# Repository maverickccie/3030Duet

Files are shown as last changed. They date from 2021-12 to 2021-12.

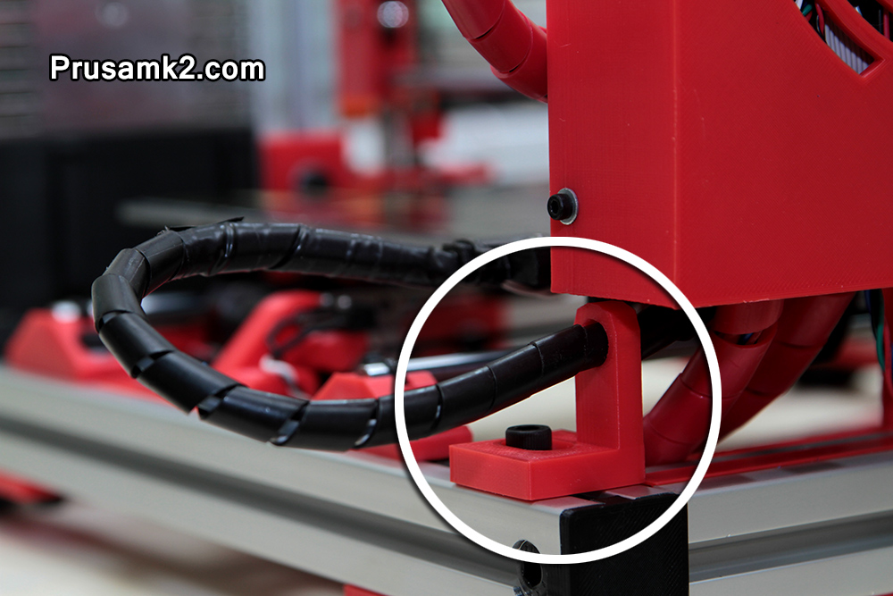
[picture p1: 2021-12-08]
Part STLs/Improved Parts from PrusaMK2.com/Haribo 3030_Cable_Guide/Photo.jpg

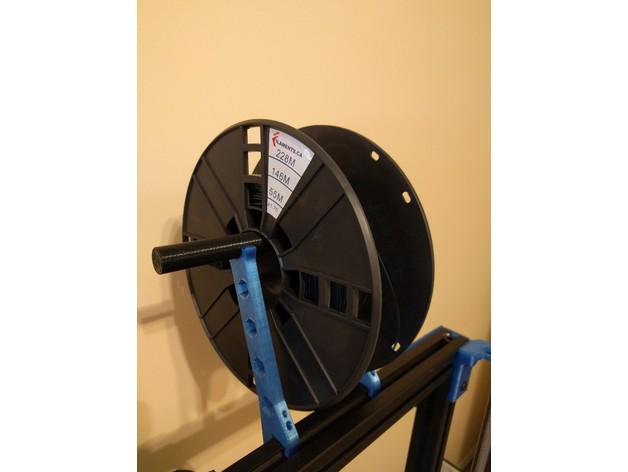
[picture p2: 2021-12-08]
Part STLs/SpoolHolders/Spool_Holder_for_3030_Extrusion/images/f4c73352651c89bbb47f65c14cc03cf2_preview_featured.jpg

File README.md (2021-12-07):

# My 3030 Duet baseed MK2.5

Better then a stock Prusa MK2.5 in so many ways

## Introduction

Welcome my project page!

## Thanks to 

### CNCKitchen

I used this his guide to move to the Duet V3 mini: https://www.cnckitchen.com/blog/prusa-mk25s-duet-3-mini-5-conversion

Dude you rock!!!!!

### Prusamk2users

The orginal conversion to Haribo 3030 came from here: https://github.com/PrusaMK2Users/3030_Haribo_Edition

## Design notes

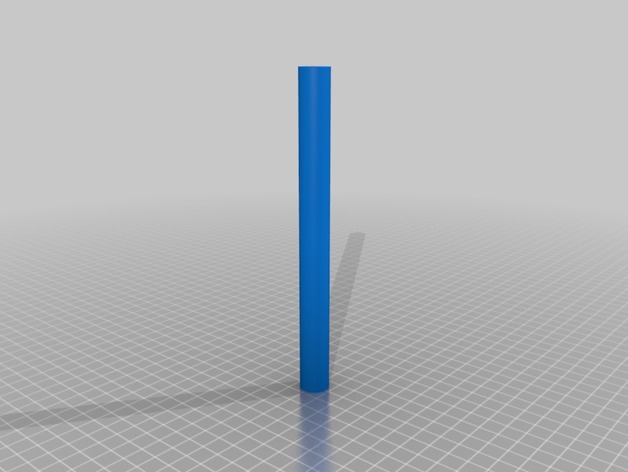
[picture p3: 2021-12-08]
Part STLs/SpoolHolders/Spool_Holder_for_3030_Extrusion/images/fe1c89c3e8150db4dd0982f04f4783a8_preview_featured.jpg

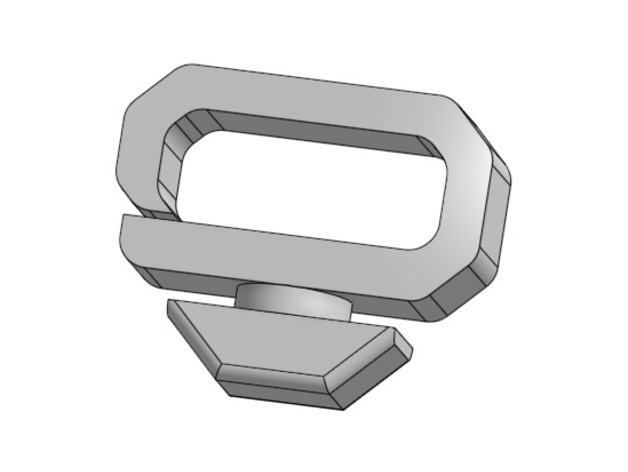
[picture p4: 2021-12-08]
Part STLs/CableClips/3030_Extrusion_Profile_Cable_Clip/images/18c306208e1527c0a5ba9f1ea7bc6678_preview_featured.jpg

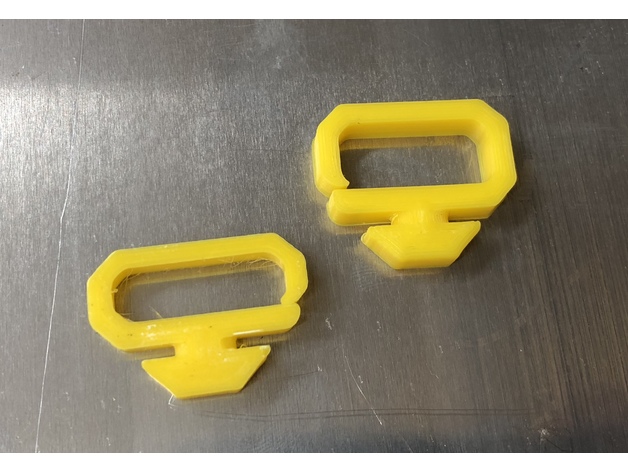
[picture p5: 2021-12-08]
Part STLs/CableClips/3030_Extrusion_Profile_Cable_Clip/images/cf8a90efcba08733e2580e20ebf21c80_preview_featured.jpg

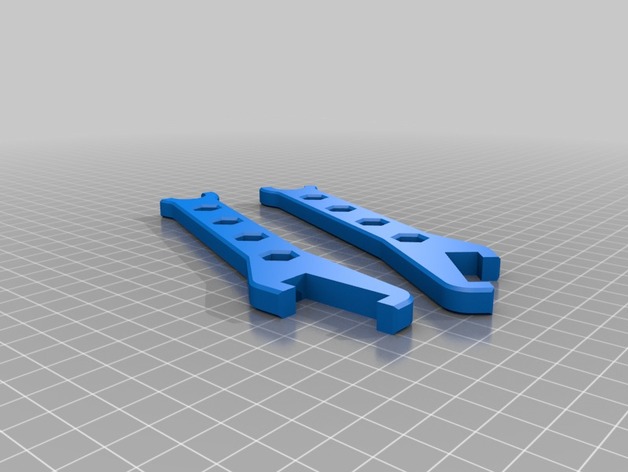
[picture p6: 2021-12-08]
Part STLs/SpoolHolders/Spool_Holder_for_3030_Extrusion/images/9926562ceaf5244885a4c4ae6ae50522_preview_featured.jpg

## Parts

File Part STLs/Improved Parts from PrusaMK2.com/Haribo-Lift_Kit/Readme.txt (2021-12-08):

These can be printed (4) and placed under each corner raising your Haribo 40mm off your work surface allowing you to easily to reach under your printer to clean up debris.

Square surface top, round surface to mate with rubber anti vibration pads.

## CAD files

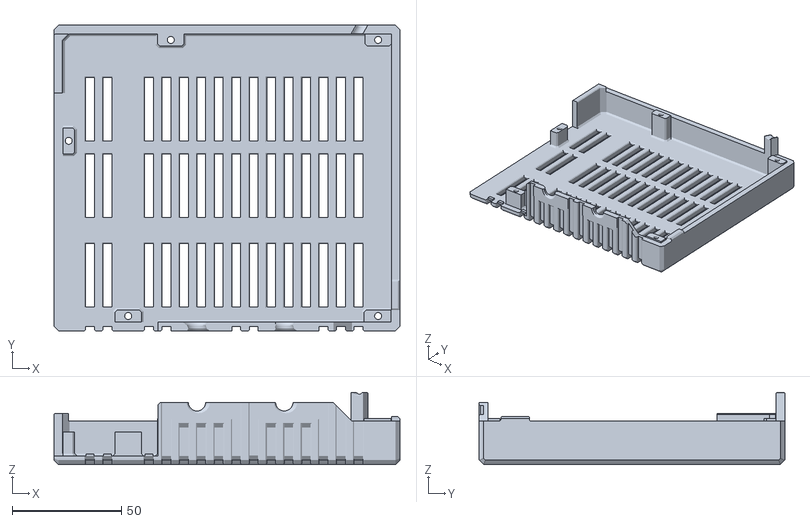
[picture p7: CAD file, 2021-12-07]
CNCKitchen/Box_Top.stl
158.5 x 140.0 x 33.0

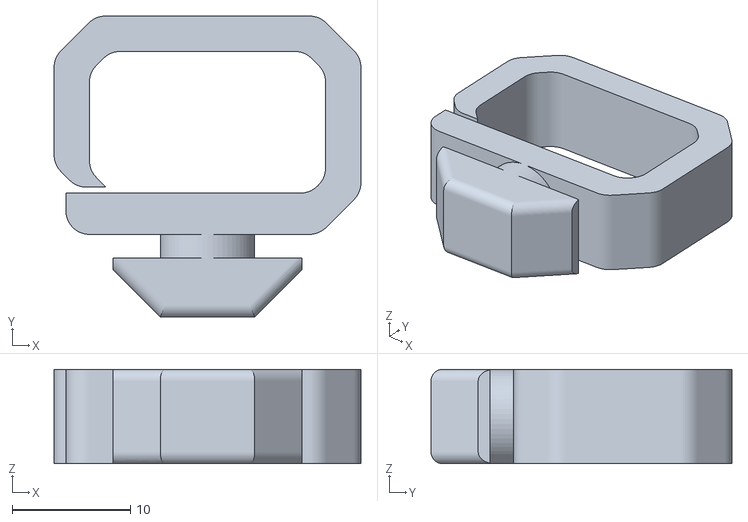
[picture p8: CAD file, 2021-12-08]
Part STLs/CableClips/3030_Extrusion_Profile_Cable_Clip/files/3030_cable_clip_12mm.stl
26.0 x 25.5 x 8.00

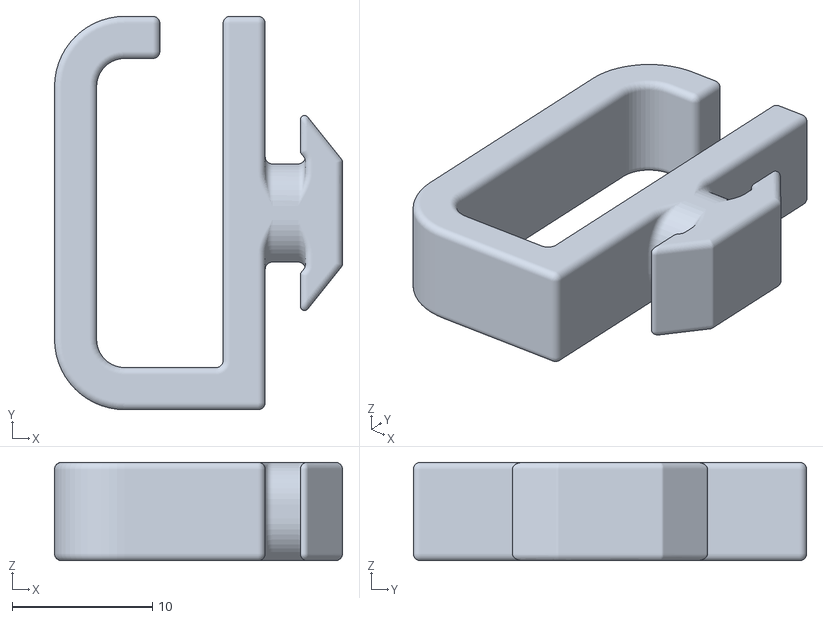
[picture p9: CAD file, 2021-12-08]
Part STLs/CableClips/Cable_clip___holder_for_3030/files/cable_clip_for_3030.STL
20.5 x 28.0 x 7.00

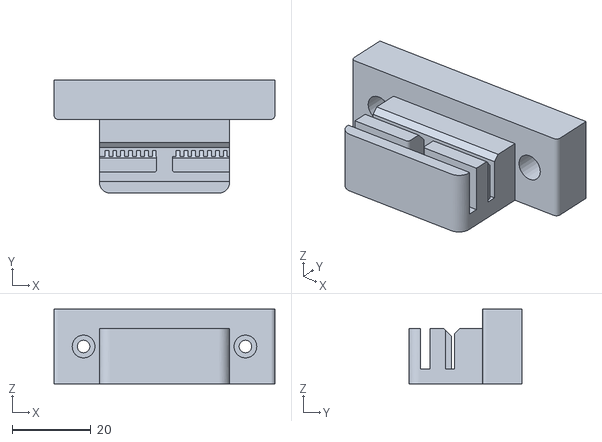
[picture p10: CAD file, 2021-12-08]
Part STLs/Improved Parts from PrusaMK2.com/1x_mk2x_y_belt_holder_modded_R2/1x_mk2x_y_belt_holder_modded_R2.stl
56.0 x 28.7 x 19.0

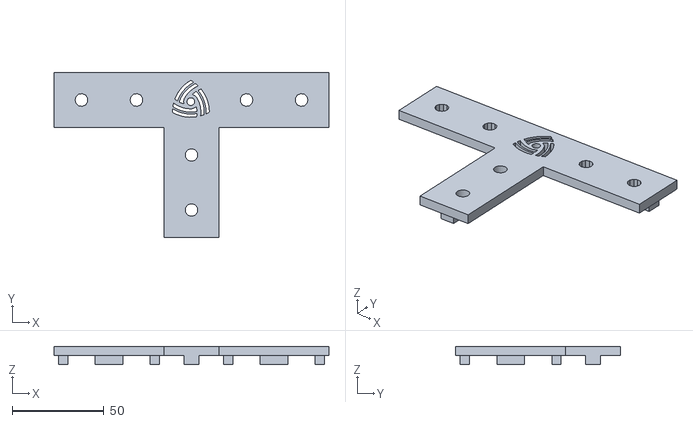
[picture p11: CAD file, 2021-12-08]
Part STLs/Improved Parts from PrusaMK2.com/2x_t_bracket_V2/2x_t_bracket_V2.stl
150.0 x 90.0 x 10.0

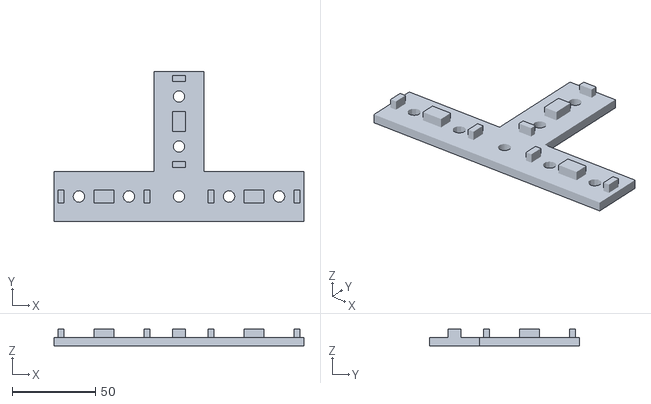
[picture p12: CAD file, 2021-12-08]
Part STLs/Improved Parts from PrusaMK2.com/2x_T_Piece_T-Sun_Nuts/2x T Piece T-Sun Nuts.stl
150.0 x 90.0 x 10.0

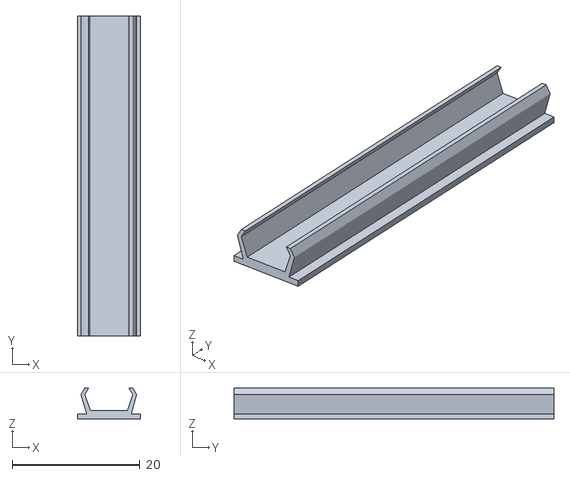
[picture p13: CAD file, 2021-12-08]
Part STLs/Improved Parts from PrusaMK2.com/3030-Channel_Cover/Channel_Cover.stl
9.80 x 50.0 x 4.82

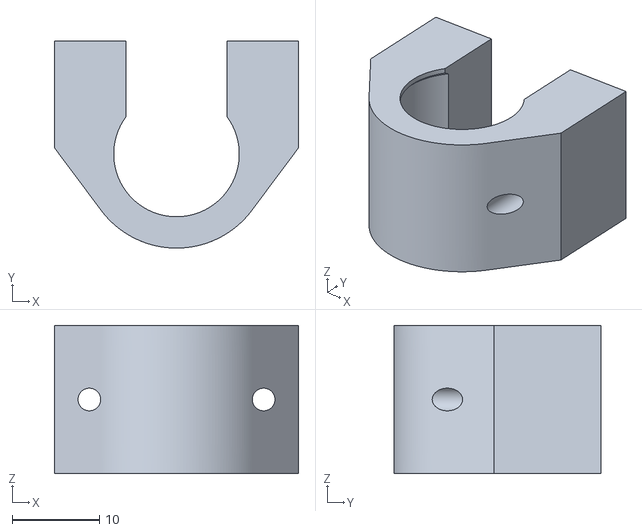
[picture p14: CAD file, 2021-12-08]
Part STLs/Improved Parts from PrusaMK2.com/3x_y_bearing_housing_PLA_IGUS/3x_y_bearing_housing_PLA_IGUS.stl
28.0 x 23.8 x 17.0

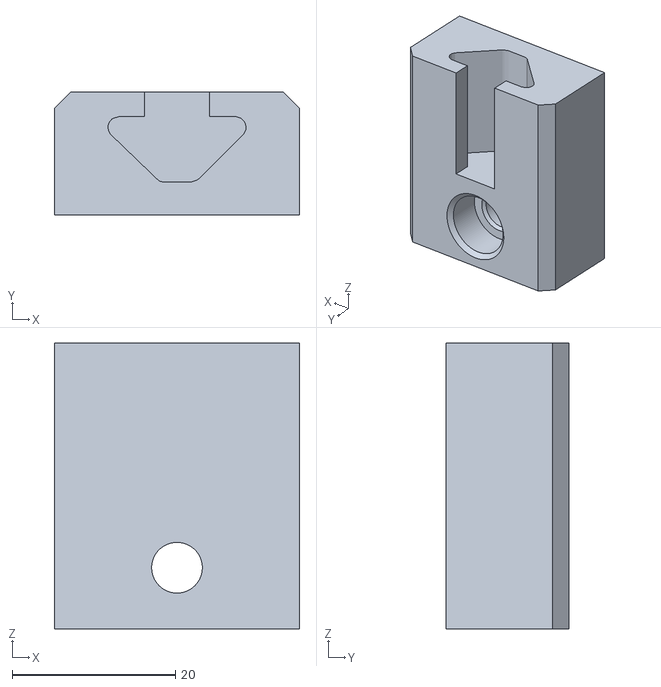
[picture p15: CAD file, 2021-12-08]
Part STLs/Improved Parts from PrusaMK2.com/External 3030 Mount/External 3030 Mount.stl
30.0 x 15.0 x 35.0

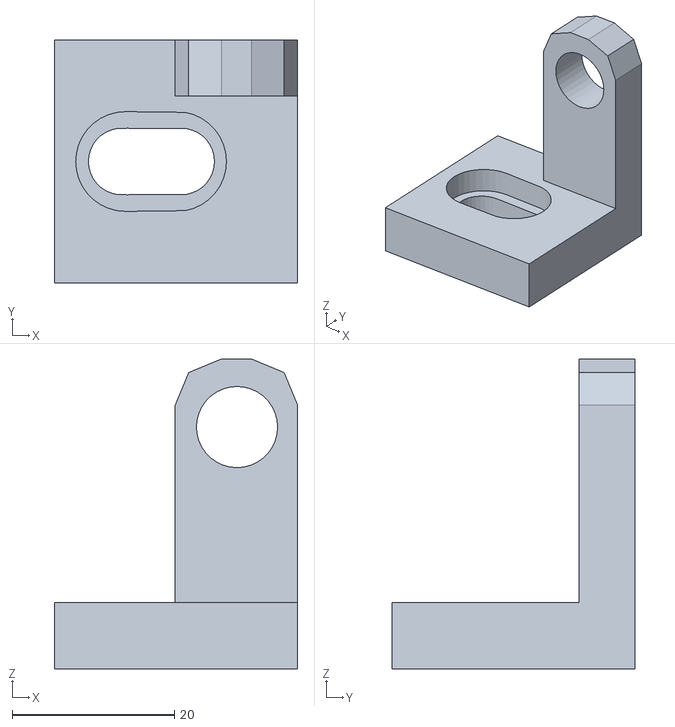
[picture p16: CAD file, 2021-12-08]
Part STLs/Improved Parts from PrusaMK2.com/Haribo 3030_Cable_Guide/Haribo 3030_Cable_Guide.stl
30.0 x 30.0 x 38.2

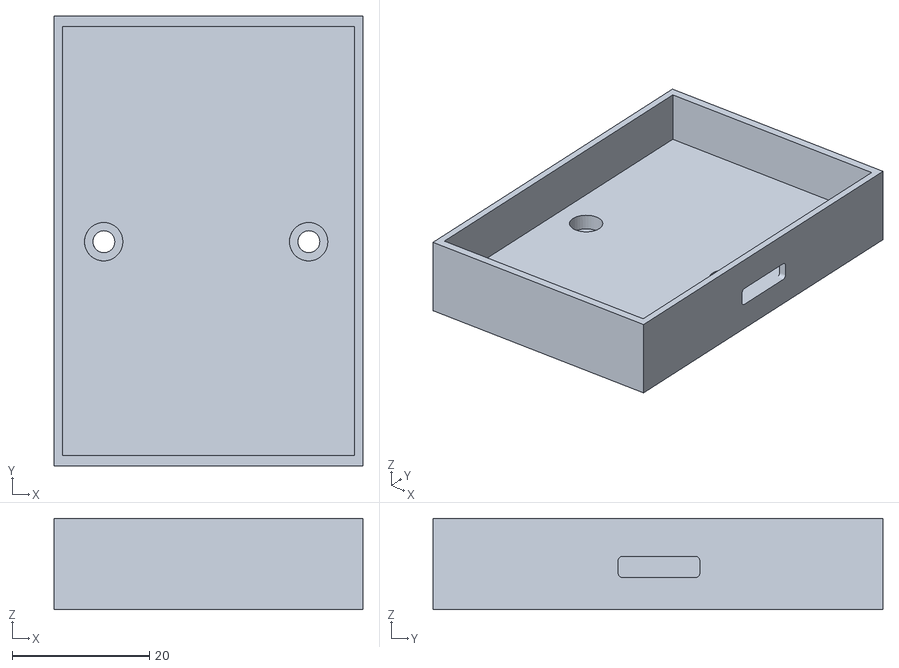
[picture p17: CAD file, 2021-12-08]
Part STLs/Improved Parts from PrusaMK2.com/Haribo LED Z Light Mounts/Led_Light_Case_side_hole.stl
45.0 x 65.5 x 13.3

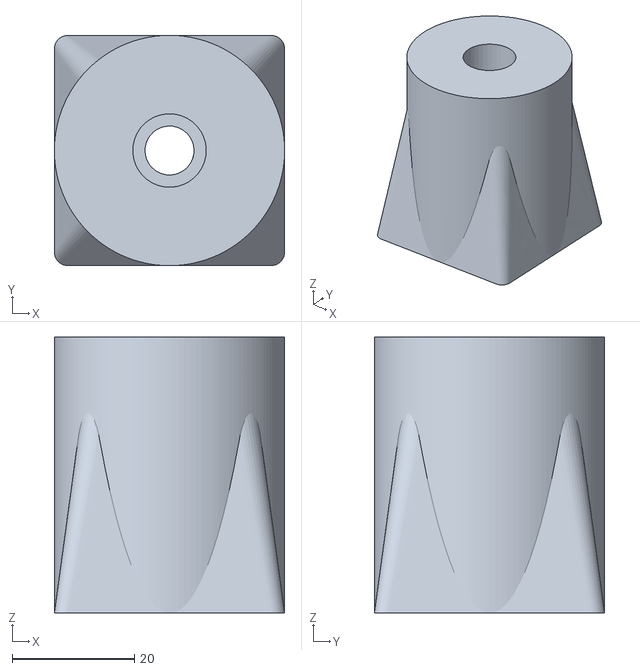
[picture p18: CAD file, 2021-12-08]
Part STLs/Improved Parts from PrusaMK2.com/Haribo-Lift_Kit/Haribo-Lift_Kit.stl
37.6 x 37.6 x 45.1

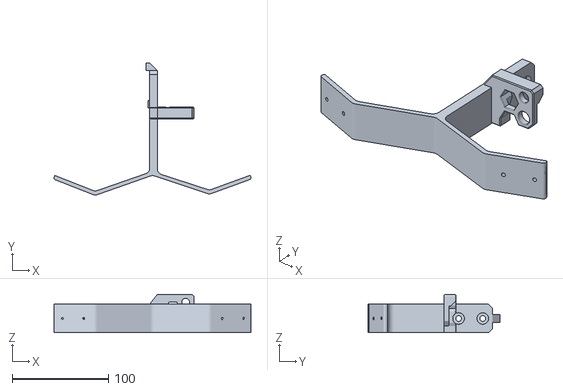
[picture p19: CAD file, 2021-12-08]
Part STLs/Improved Parts from PrusaMK2.com/Haribo_3030_Double_LED_Light_Bracket/files/Right_Bracket.stl
204.6 x 137.2 x 40.0

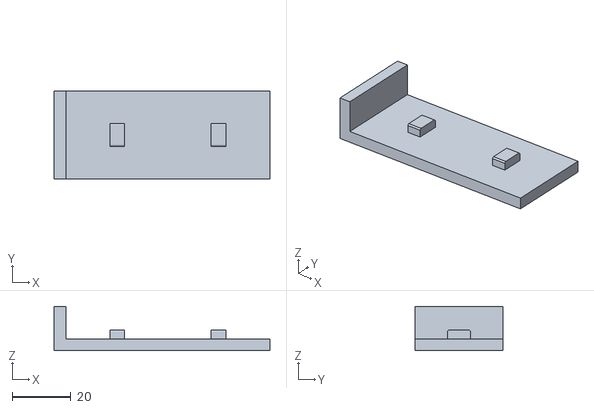
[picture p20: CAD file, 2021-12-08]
Part STLs/Improved Parts from PrusaMK2.com/Haribo_Perp/Haribo_Perp.stl
73.5 x 30.0 x 15.0

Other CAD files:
Part STLs/Improved Parts from PrusaMK2.com/Haribo_Y_Motor_brace_block/Haribo_Y_Motor_brace_block.stl
Part STLs/Improved Parts from PrusaMK2.com/Haribo_Z_Mount_LED_Brackets_Tall_Version/Haribo_Z_LCD_Bracket.stl
Part STLs/Improved Parts from PrusaMK2.com/Linear_Bearing_Brackets/Linear_Bearing_Brackets.stl
CNCKitchen/Box_Bottom.stl
CNCKitchen/CableClamp1.stl
CNCKitchen/CableClamp3.stl
Part STLs/CableClips/3030_Extrusion_Profile_Cable_Clip/files/3030_cable_clip_8mm.stl
Part STLs/Improved Parts from PrusaMK2.com/8mm_lead_screw_Nut/8mm_lead_screw_Nut.stl
Part STLs/Improved Parts from PrusaMK2.com/8mm_lead_screw_Nut/trapezoidal_nut_T8x2_for_printing_with_nylon_bridge.STL
Part STLs/Improved Parts from PrusaMK2.com/8mm_lead_screw_Nut/trapezoidal_nut_for_printing_with_nylon_bridge.STL
Part STLs/Improved Parts from PrusaMK2.com/Haribo LED Z Light Mounts/Haribo_Z_LCD_Mount_LEFT_Tall.stl
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

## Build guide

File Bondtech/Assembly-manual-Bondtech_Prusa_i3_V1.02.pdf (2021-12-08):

# Bondtech for Prusa i3

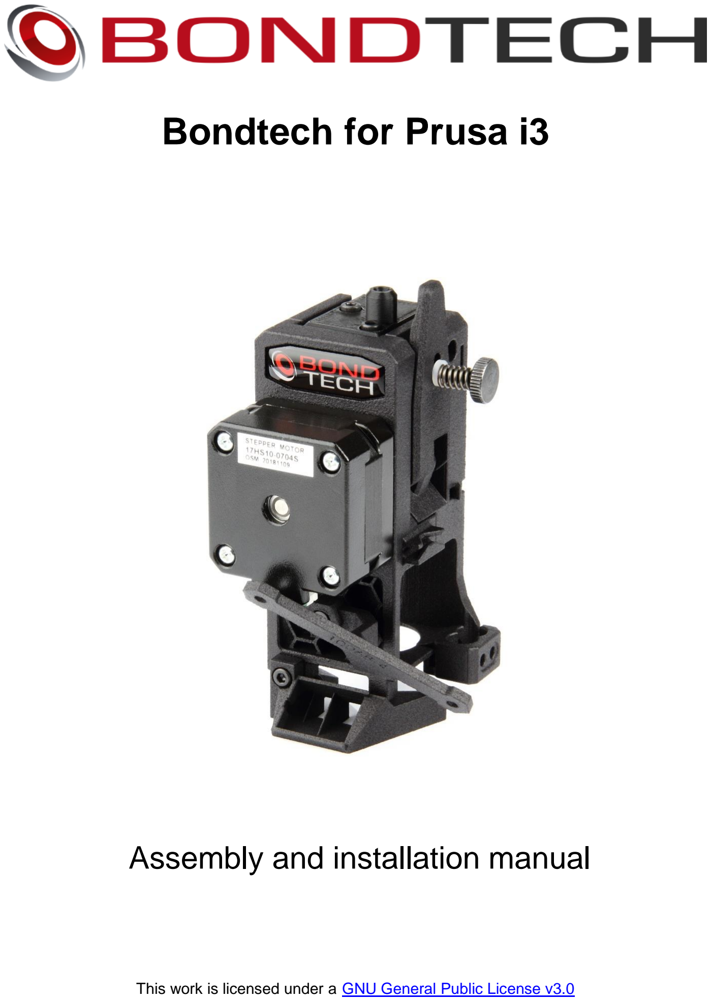
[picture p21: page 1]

## Assembly and installation manual

This work is licensed under a GNU General Public License v3.0 (https://www.gnu.org/licenses/gpl-3.0.html)

Installation manual extruder upgrade for Bondtech_Prusa_i3 V1.02

## Table of Contents

Acknowledgements | 1
Introduction | 1
Compatibility | 2
What’s in the box? | 2
Mechanical Installation | 3
What you need | 3
Preparation | 3
Software Configuration | 15
Set new E-step value | 15

## Acknowledgements

This is a co-development work with awesome guys in the Prusa Community like Chris Warkocki, Grégorie Saunier (Bear Upgrades), Olof Ogland, Erik Bjorgan, Josh Jones, Kyle Wiehe, Marc Evertz, Matt Harrison, Ocie Ward, Sando Bendig, Vecko Kojchevski (Vecko Extruder), Steven Mölby that have provided excellent feedback and suggestions of how to develop the "perfect" extruder setup for the Prusa series printer. A lot of work has been spent in this project and we have tried to listen to all the inputs in order to find a solution that can be fitted to a Prusa I3 MK2, MK2S, MK2.5 and MK3.

## Introduction

This kit contains the necessary parts to convert to our freshly designed extruder that uses 3:1 gearing ratio for improved precision and resolution, optimized geometry for the heat-sink cooling and many other improved features.
It also reduces the moving weight to reduce vibrations and ghosting.

## Compatibility

The upgrade is compatible with the following machines:

- Prusa i3 MK2
- Prusa i3 MK2s
- Prusa i3 MK2,5
- Prusa i3 MK3

## What’s in the box?

All customers

1x Bondtech extruder for Prusa i3. 1x PTFE tube (80mm).
1x SLS printed Extruder front.
1x SLS printed Extruder rear.
1x Bag with screws and bolts. 1x Fan shroud.
1x Mounting bracket.

MK2, MK2s, MK2.5 and MK3 without BMG

1x Nema17 Pancake stepper motor.
1x Stepper motor cable.
1x Shaft with 50T gear.
1x Thumbscrew.
2x Ball bearings.
1x 3x32mm shaft.
1x Sensor cover

MK2 and Mk2s

2x Needle bearing.
1x 3x20mm shaft.
1x Primary drive wheel (direct). 1x Secondary drive wheel (direct). 1x Sensor cover

## Mechanical Installation

## What you need

To install the upgrade you will need.
- M1.5- Hex Wrench
- M2.5- Hex Wrench
- Hobby knife with sharp tip or similar.

Recommended: Download and print out Bondtech’s PTFE fixture for precise measurement of the tube length. STL-file available at https://github.com/BondtechAB/Bondtech_Prusa_i3/tree/master/CAD-Files

## Preparation

Remove your old extruder. Use Prusa’s extruder assembly guide to reverse the steps if you need to. This kit will use a different motor, so you can unwrap the cables, remove your current motor to prepare for a new one.

- Preparing your motor.

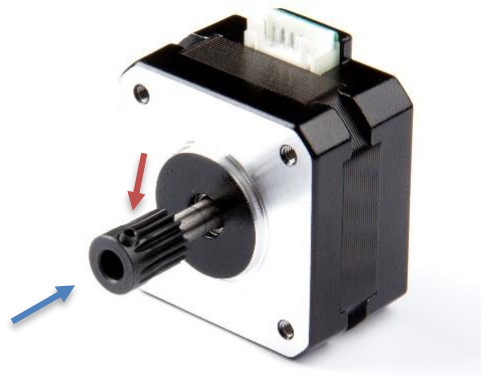
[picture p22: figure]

- Insert the M2x3 setscrew and slide the motor gear onto the shaft as oriented in the picture.

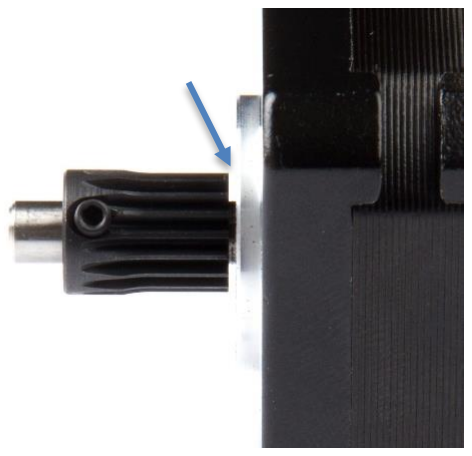
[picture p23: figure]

- Leave a 1-1,5 mm gap between the gear and the motor and tighten it using your 1,5mm Allen key.

Recommended: Use Loctite to secure the screw.

- Assembly the extruder front. Make sure the pre-assembled M3 Hex nut is mounted and fixed in the front piece of the extruder body.

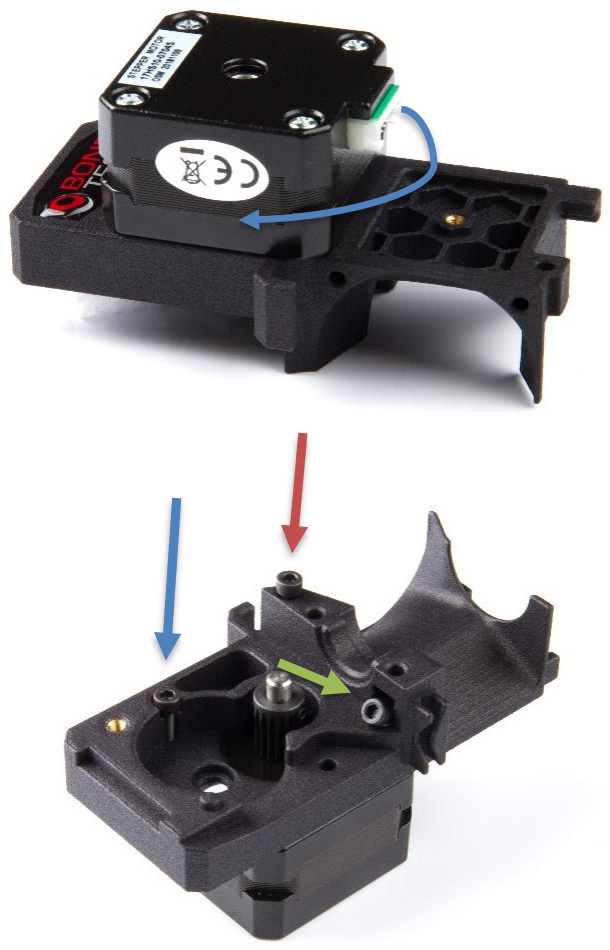
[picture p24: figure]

- Place the motor on the extruder front and orient the cable connection as you choose.
(Downwards or to the left.)

- Insert three M3 screws and loosely tighten them using a 2.5mm Allen key.
- M3x8
- M3x12
- M3x25

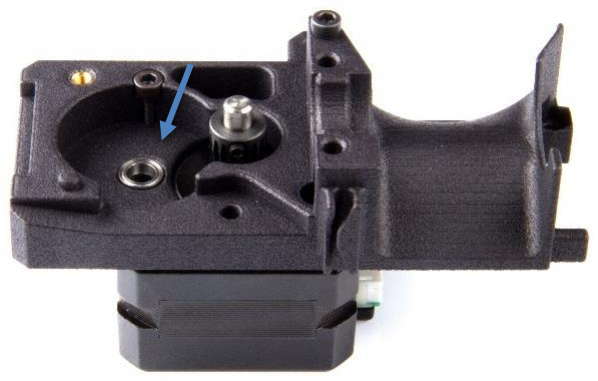
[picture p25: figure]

- Insert a ball bearing. Ensure it is fully pressed down into the slot.
- Insert the shaft with the white plastic gear into the bearing. Rotate the shaft to ensure correct alignment of the gears.

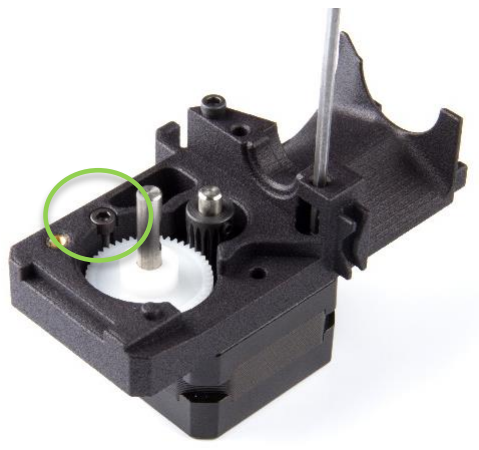
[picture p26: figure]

- Tighten the screws with
reasonable force.
- Important: Be careful
when tighten the M3x12
screw to avoid damaging
the pocket!

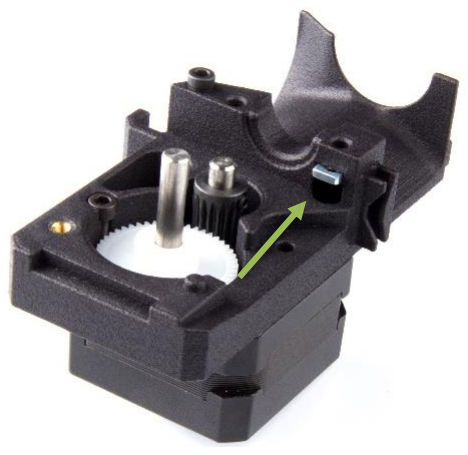
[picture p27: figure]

- Insert a square nut into the pocket.
- Prepare the extruder rear. Insert a ball bearing and press it down using a primary drive gear.
- If you are using the bear X-carriage remove hex cover plug by pushing it from the rear side. This hole is for a M3 nut.

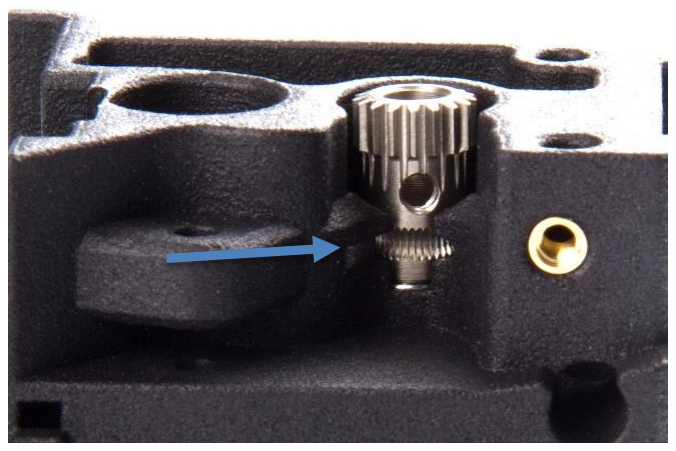
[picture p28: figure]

- Press the primary drive gear down until the groves align with the filament path.

- Slide the shaft inside the drive gear. Note the orientation of the parts. The hole and the flat surface on the shaft must align.

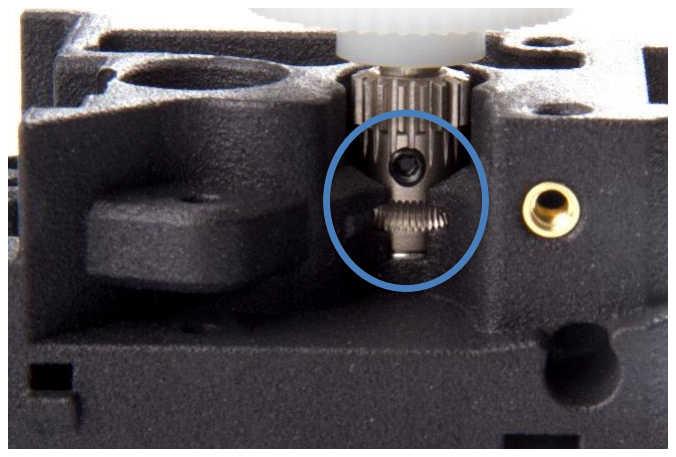
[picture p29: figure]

- Insert the M3x2 setscrew and tighten it with your 1,5 Allen key.

Important: Ensure the groves align with the filament path!

Recommended: Use Loctite to secure the screw.

Important: If the setscrew is not properly aligned with the flat surface it will stick out and start grinding on the
secondary drive gear when you start printing!

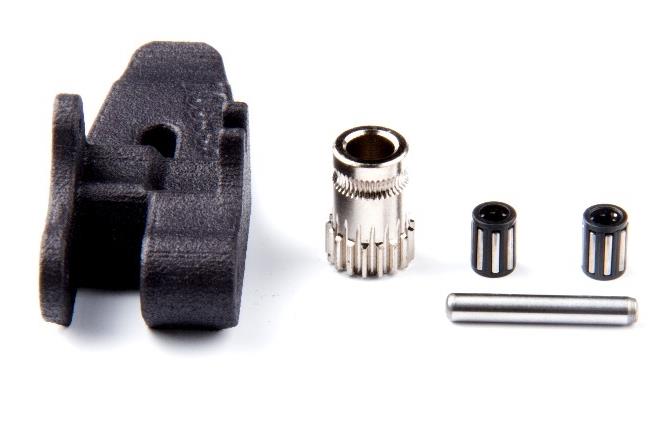
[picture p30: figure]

- Assemble the hinge.

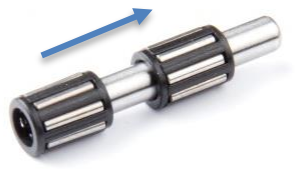
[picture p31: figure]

- Slide the two needle bearings onto the 3x20 mm shaft.
- Use a small dab of lithium based grease to lubricate the bearings
- Slide the shaft with the bearings through the secondary drive gear.
- Align the gear with the hinge as shown in the photo and press the shaft down until you hear the click.
- Carefully press the shaft in place using your 2.5mm Allen key.
- Put a small dab of lithium based grease on the gear section to reduce friction. Make sure that you do not get it on the drive section of the gear.

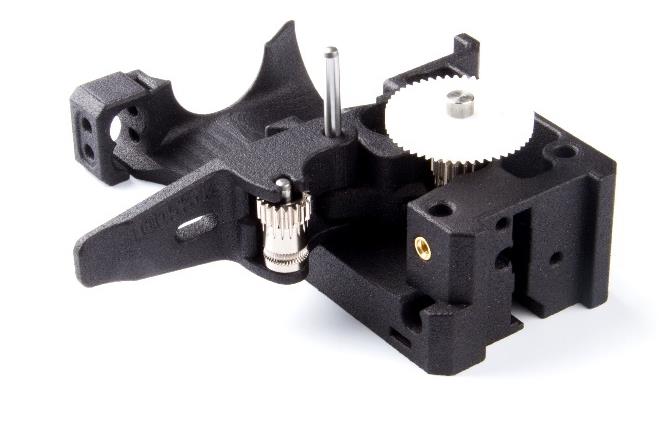
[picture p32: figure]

- Install the hinge to the extruder rear using the 3x32mm shaft.

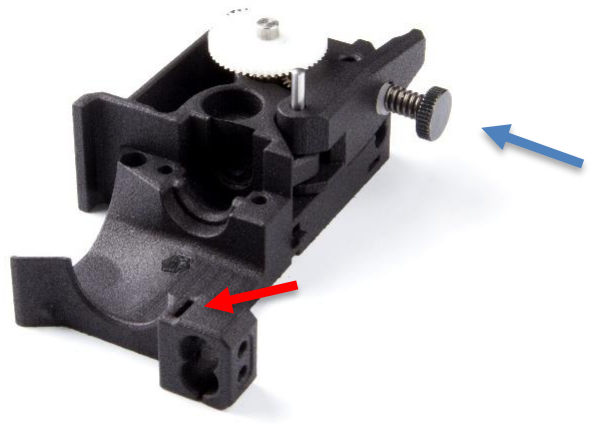
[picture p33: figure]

- Install the thumbscrew.
- If you are a MK2/s user
insert a square nut in the front pocket for the Pinda Probe.
- Prepare the HotEnd. Take the new supplied PTFE tube. Cut one of the ends according to Prusas recommendation, using a knife or a razor. Using this fixture (https://www.thingiverse.com/thing:3344656) will help. (Credits to Olof Ogland)
- Insert the newly cut end of the tube into the HotEnd.

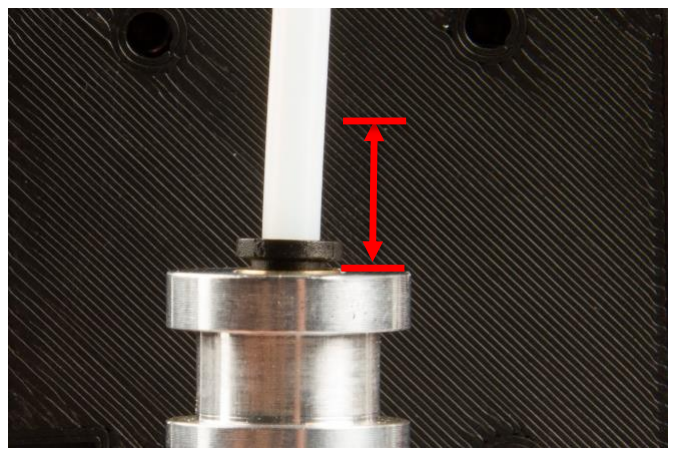
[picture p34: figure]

- Cut the tube 6.3 mm from the top of the HotEnd. Save the
remaining piece for the sensor cover.

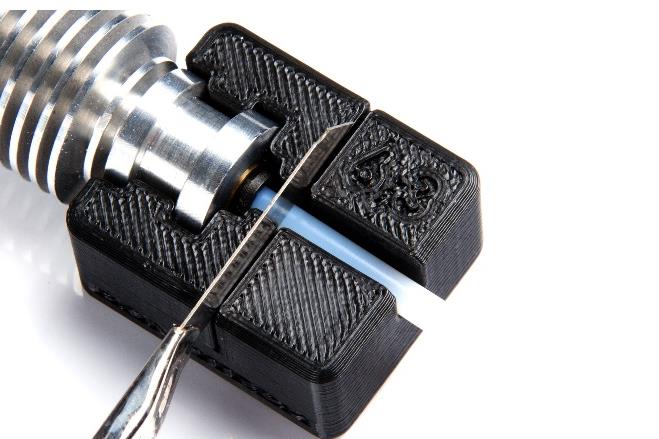
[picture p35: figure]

- Recommended: Use Bondtech’s cutting fixture for precise measurement. STL-file is
available at:
https://github.com/BondtechAB/Bondtech_Prusa_i3/tree/master/C AD-Files (https://github.com/BondtechAB/Bondtech_Prusa_i3/tree/master/CAD-Files)
- Use a knife or razor to chamfer the inside of the tube for better filament guidance.

Important: Do not let any left over from the tube fall into the HotEnd we recommend you
remove the tube before
chamfer the inside!
- Insert a push fit clip between the HotEnd and the collet.
- Recommended: Add a small piece of tape, 5x20mm on the inner ring. The low friction between the parts may cause the HotEnd to rotate to easily when installed.

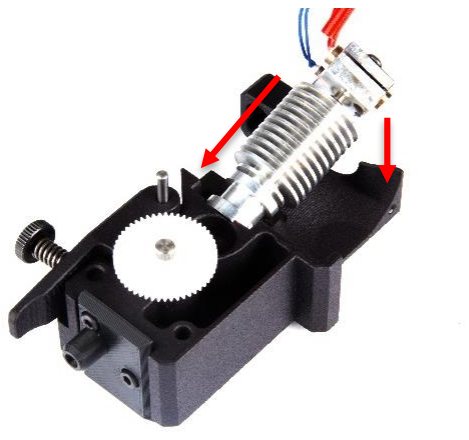
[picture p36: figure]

- Install the HotEnd into the extruder rear, angled as shown in the photo. And push it in place.

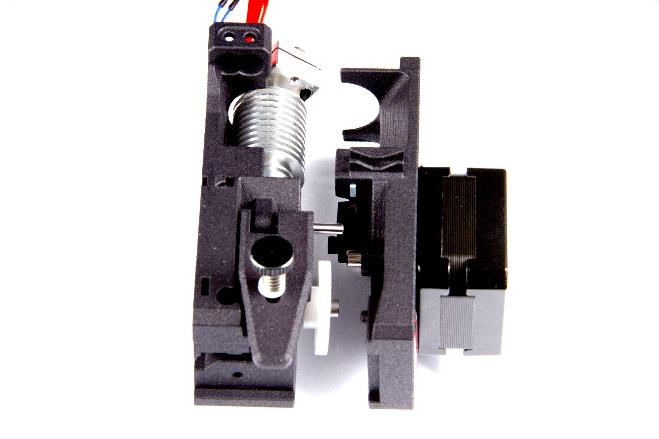
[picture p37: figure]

- Attach the front onto the rear part. Push the HotEnd upwards to align the neck correctly.
- Ensure everything is aligned and carefully clamp the parts
together.

Important: The parts should fit together easy. Do not use any excessive force!

- Install the extruder to your X-Carriage using three M3 screws.
- M3x40
- M3x45

Important: These screws are sized to use on your stock MK2,5/MK3 carriage or the
modified MK2/s carriage. If you have another carriage different screw length could be
necessary!

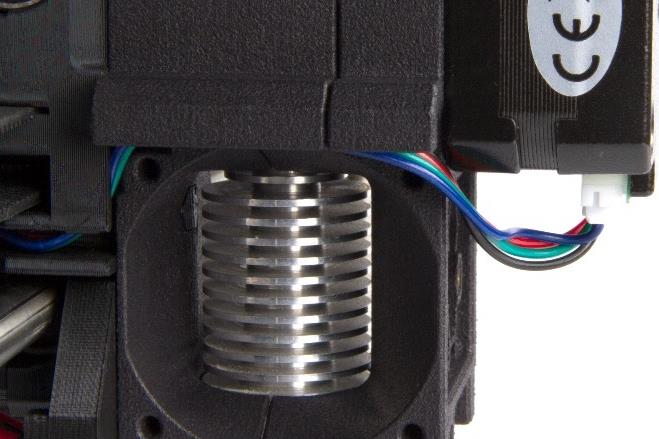
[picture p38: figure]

- Connect the cable to the motor and use the cable path to the left of the extruder for guidance.

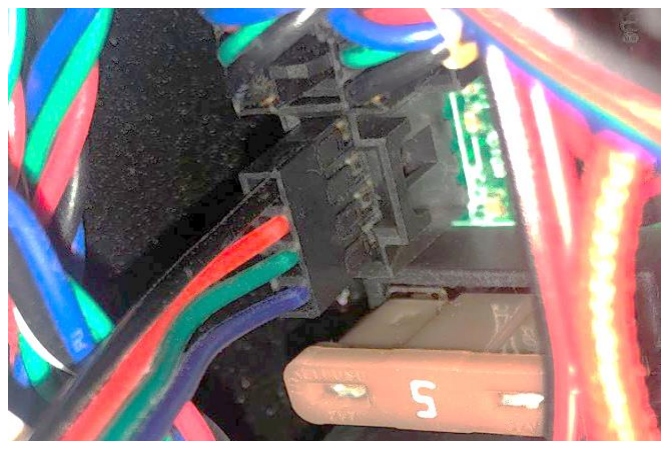
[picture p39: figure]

- When connecting the cable to you board ensure the black cable is the top most cable or the motor will rotate the wrong way!

- Install your 40x40 fan using four M3x12 screws.

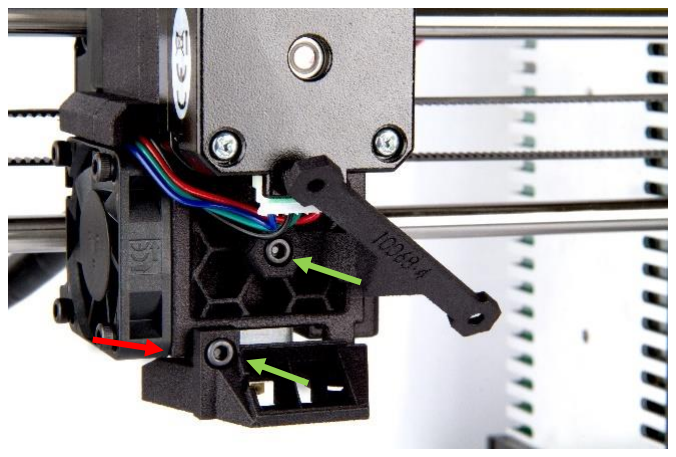
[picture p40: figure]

- Install the mounting bracket using a M3x10 screw. Place a M3 hex nut in the pocket and tightened the fan shroud using a M3x10 screw.
- M3x10
- M3 hex nut

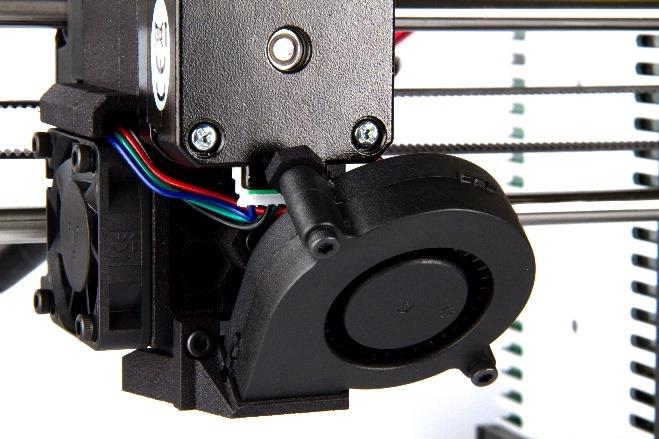
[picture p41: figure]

- Place two hex nuts into the slots on the mounting bracket and slide your 5015-blower fan down the fan shroud and mount it using two M3x20 screws.
- Place the cable in the channel on the right side of the extruder to help guide the way.
- The position of the P.I.N.D.A probe depends on your version of the printer. MK2/s users place the probe to right (Closer to the X-axis) MK2.5 and MK3 users place the probe to the left (furthest away from the X-axis).

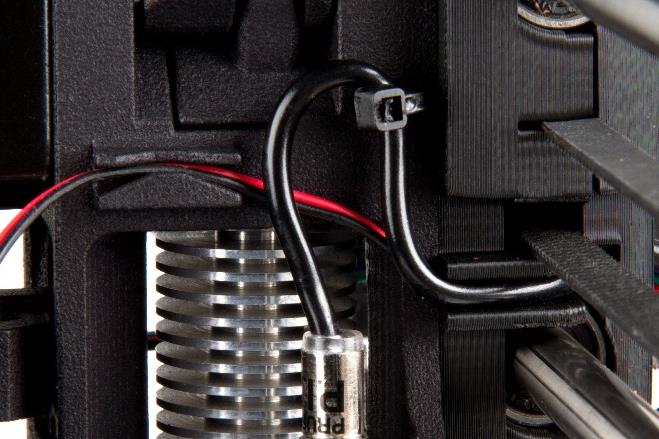
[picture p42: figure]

- Optional P.I.N.D.A cable position. This technique is developed by Grégoire Saunier, creator of the Bear Extruder, to improve air flow and reduce turbulence. Check out his work here: (https://github.com/gregsaun)

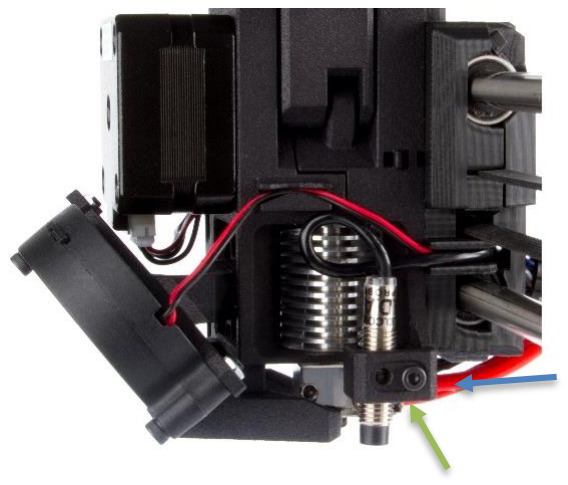
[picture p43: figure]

- MK2.5, MK3 users insert a square nut into the right slot (MK2s in the left as shown earlier). Secure the P.I.N.D.A using a M3x16 screw.
- Square nut
- M3x16

Reminder: Adjust the height of the probe according to Prusa’s instructions.

- Cut a 14.5mm long piece of the left-over PTFE Tube and insert it into the filament path on top of the extruder.

Recommended: Before inserting the tube use a knife or razor to chamfer the inside of the tube for better filament guidance.

- If you have a filament sensor install it according to Prusa’s instructions.

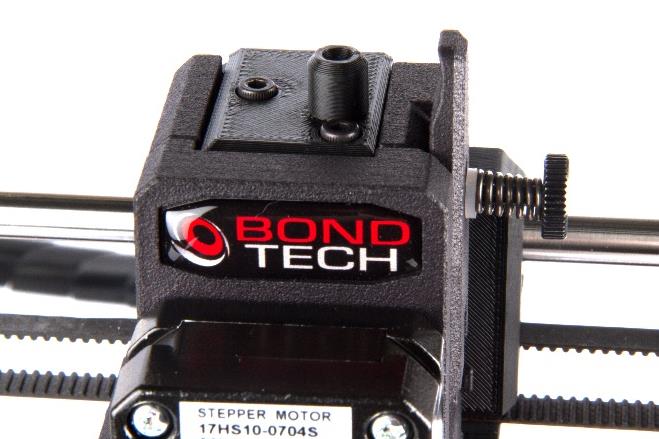
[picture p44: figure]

- Place the sensor cover on top and fasten it using two M3x8 screws.

## Software Configuration

As the new extruder uses a gear reduction to create a high extrusion resolution and high torque the E-step value needs to be changed. The E-step value tells the printer how many steps to send to the motor for each mm of filament.

## Set new E-step value

The E-step value is set using a G-code file that you can download here: (https://github.com/BondtechAB/Bondtech_Prusa_i3/tree/master/GCODE)
These files are used to set the new E-step value on the printer. On MK2, MK2S and MK2.5 the E-step value should be 415 as it uses 16-bit microstepping, on MK3 it shall be 830 as it uses 32-bit microstepping, this is valid for standard 1.8 degree stepper motors, if a 0.9 degree motor is used the E-step needs to be doubled, so 830 and 1660.

Copy the file to the SD-card and put it in the printer, select to print the file and the new e-step value will be set and saved to the controller.

Good luck with your Bondtech feeder!

If you have any questions please first read the FAQ (http://www.bondtech.se/en/faq/). If the question still hasn’t been answered feel free to contact us by email or our online chat.

Repslagarvägen 3 J
33153 Värnamo
Sweden

e-mail: support@bondtech.se phone: +46702220193
paypal: payments@bondtech.se
web: www.bondtech.se
VAT-registration number: SE556995564301

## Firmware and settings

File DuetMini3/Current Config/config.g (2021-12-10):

; Configuration file for Duet 3 Mini 5+ (firmware version 3)
; executed by the firmware on start-up
;
; generated by RepRapFirmware Configuration Tool v3.2.3 on Mon Mar 15 2021 19:09:36 GMT+0100 (Mitteleuropäische Normalzeit)

; ##### General preferences
G90                                          						; send absolute coordinates...
M83                                          						; ...but relative extruder moves
M550 P"Prusa MK2.5S DUET"                          					; set printer name
;M575 P1 B57600 S1													; PannelDue Comm setup

; ##### Network
M552 S1                                      						; enable network
M586 P0 S1                                   						; enable HTTP
M586 P1 S1                                             				; enable FTP
M586 P2 S0                                   						; disable Telnet

; ##### Drives
M569 P1 S0 D3 V10                                					; X drive @1
M569 P2 S0 D3 V10                                					; Y drive @2
M569 P0 S0 D3 V100                               					; Z left drive @0
M569 P4 S0 D3 V100                               					; Z right drive  @4
M569 P3 S1 D3 V1000                               					; E drive @3 - inversed
M584 X1 Y2 Z0:4 E3                     								; set drive mapping
M671 X-37:287 Y0:0 S10                                     			; define dual driven z-axis 

M350 X16 Y16 Z16 E32 I1                      						; configure microstepping with interpolation
M92 X100.00 Y100.00 Z400.00 E830.00             					; set steps per mm
M566 X600.00 Y600.00 Z48.00 E300.00        							; set maximum instantaneous speed changes (mm/min)
M203 X8000.00 Y8000.00 Z720.00 E7200.00      						; set maximum speeds (mm/min)
M201 X1250.00 Y1250.00 Z1250.00 E2000.00        					; set accelerations (mm/s^2)
M906 X750 Y750 Z600 E700 I30                						; set motor currents (mA) and motor idle factor in per cent
M84 S30                                      						; Set idle timeout

; ##### Axis Limits
M208 X0 Y-4 Z0 S1                             						; set axis minima
M208 X255 Y212.5 Z222.5 S0                       					; set axis maxima

; ##### Endstops
M574 X1 S1 P"io0.in"                        						; X endstop
;M574 X1 S1 P"io3.in"                        						; X endstop if the PannelDue is used
M574 Y1 S1 P"io1.in"                        						; Y endstop

; ##### Filament Sensor
; M591 D0 P2 C"io3.in" S1                                    		; Filament Runout Sensor

; ##### Z-Probe Settings for PINDA 2
M558 P5 C"io2.in" I1 H3 F1000 T6000 A3              				; Prusa PindaV2 Endstop
M308 S2 P"temp2" A"Pinda V2" Y"thermistor" T100000 B3950      		; Prusa PindaV2 Thermistor
G31 P1000 X23 Y5 Z1.4                                  				; Nozzle offset
M574 Z1 S2                                                 			; Set Z axis endstop, controlled by probe
M557 X24:228 Y6:210 P7                                    			; Define mesh grid for probing
M376 H5																; Fade height 5mm

; ##### Heaters
; Bed Heater
M308 S0 P"temp1" Y"thermistor" B4725 C7.060000e-8 					; configure sensor 0 as thermistor on pin temp1
M950 H0 C"out0" Q25 T0                           					; create bed heater output on out0 and map it to sensor 0, PWM frequency: 25Hz
M307 H0 R0.262 C338.0 D10.52 S1.00 V11.8 B0							; Bed tuning values, enable PID
M140 H0                                                    			; Bed uses Heater 0
M143 H0 S120                                               			; Set temperature limit for heater 0 to 120C Bed
; Hotend heater
M308 S1 P"temp0" Y"thermistor" B4725 C7.060000e-8 					; configure sensor 1 as thermistor on pin temp0
M950 H1 C"out1" T1                           						; create nozzle heater output on out1 and map it to sensor 1
M307 H1 B0 S1.00                             						; disable bang-bang mode for heater  and set PWM limit
M143 H1 S295                                 						; set temperature limit for heater 1 to 295C
M302 S170 R170                                         				; allow extrusion starting from 170°C and retractions already from 170°C

; ##### Fans
; Part cooling fan
M950 F0 C"out3" Q100                         						; create fan 0 on pin out3 and set its frequency
M106 P0 S0 H-1                               						; set fan 0 value. Thermostatic control is turned off
; Hotend cooling fan
M950 F1 C"out6" Q5000												; NOCTUA fan an pin out6 with 5000Hz PWM frequency
M106 P1 T55 S255 H1  												; Temperature control: turn fan on at 55°C

; ##### Tools
M563 P0 D0 H1 F0                             						; define tool 0
G10 P0 X0 Y0 Z0                              						; set tool 0 axis offsets
G10 P0 R0 S0                                 						; set initial tool 0 active and standby temperatures to 0C
M572 D0 S0.06								 						; Pressure Advance

; ##### Startup
M18 XYE                                                				; release / unlock X, Y, and E axis
M501                                                   				; use config-override (for Thermistor Parameters and other settings)
G90                                                    				; send absolute coordinates...
M83                                                   				; ... but relative extruder moves

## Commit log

2021-12-07 Int
    Int
    [bed.g, cancel.g, config-override.g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]
2021-12-07 Add
    Add CNC Kitchen files and thanks
    [Box_Bottom.stl, Box_Top.stl, CableClamp1.stl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]
2021-12-08 Add Files
    Add files and org changes
    [1x_mk2x_y_belt_holder_modded_R2.stl, 2x T Piece T-Sun Nuts.stl, 2x_t_bracket_V2.stl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]
2021-12-10 Change esteps and endstop pins
    Needed to change the x endstop to be able to use the PanelDue 5, Change esteps and microsteping on extruder
    [config.g]
